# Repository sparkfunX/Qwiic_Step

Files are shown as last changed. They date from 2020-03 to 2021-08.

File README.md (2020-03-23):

SparkX Qwiic Step
========================================

Qwiic Step (https://cdn.sparkfun.com/assets/parts/1/4/5/9/9/15951-Qwiic_Step-01.jpg)

Qwiic Step System (https://cdn.sparkfun.com/assets/parts/1/4/5/9/9/15951-Qwiic_Step-05.jpg)

[*SparkX Qwiic Step (SPX-15951)*](https://www.sparkfun.com/products/15951)

Qwiic Step features the A4988 stepper motor driver IC. Send commands using the I2C bus to configure your stepper motor movements. Easily attach and set up a limit switch or E-Stop and use our new favorite latching terminals to solderlessly and screwlessly attach motor and power.

Repository Contents
-------------------

* **/Documentation** - Data sheets, additional product information
* **/Firmware** - Firmware used on Qwiic Step
* **/Hardware** - Eagle design files (.brd, .sch)
* **/Production** - Production panel files (.brd)

Documentation
--------------
* **[SparkFun Qwiic Step Arduino Library](https://github.com/sparkfun/SparkFun_Qwiic_Step_Arduino_Library)** - Arduino library for the SparkX Qwiic Step.
* **[SparkFun Fritzing repo](https://github.com/sparkfun/Fritzing_Parts)** - Fritzing diagrams for SparkFun products.
* **[SparkFun 3D Model repo](https://github.com/sparkfun/3D_Models)** - 3D models of SparkFun products. 
* **[SparkFun Graphical Datasheets](https://github.com/sparkfun/Graphical_Datasheets)** -Graphical Datasheets for various SparkFun products.

License Information
-------------------

This product is _**open source**_! 

Please review the LICENSE.md file for license information. 

If you have any questions or concerns on licensing, please contact technical support on our [SparkFun forums](https://forum.sparkfun.com/viewforum.php?f=152).

Distributed as-is; no warranty is given.

- Your friends at SparkFun.

_<COLLABORATION CREDIT>_

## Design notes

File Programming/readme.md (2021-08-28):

Programming Qwiic Step
===========================================================

The Qwiic Step uses the ATmega328P with the standard Arduino/STK500 bootloader. New firmware can be loaded with a USB to serial connection and a 6-pin header.

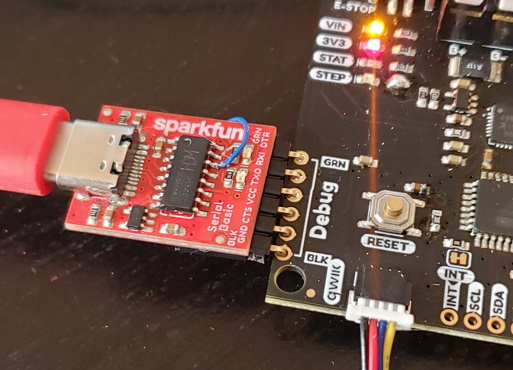
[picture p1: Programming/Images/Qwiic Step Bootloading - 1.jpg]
Programming Qwiic Step via 6-pin Serial


1) Solder a 6-pin [right angle](https://www.sparkfun.com/products/553) (or [straight](https://www.sparkfun.com/products/116)) male header onto the 'Debug' footprint.
2) Connect a [USB to Serial](https://www.sparkfun.com/products/15096) adapter along with a [USB cable](https://www.sparkfun.com/products/15425) to a computer and verify the new COM port is displayed. For information about drivers or COM port locating, see [here](https://learn.sparkfun.com/tutorials/sparkfun-serial-basic-ch340c-hookup-guide).
3) Download the contents of the 'Programming' folder so that you have **avrdude.exe**, **avrdude.conf**, **program_qwiic_step.bat**, and **Qwiic-Step-vXX.hex** in a folder.
4) Modify 'program_qwiic_step.bat' to use the COM port that your computer uses (default is COM5).
5) Open a command line, navigate to 'program_qwiic_step.bat' and run. 
6) Press enter to begin programming.

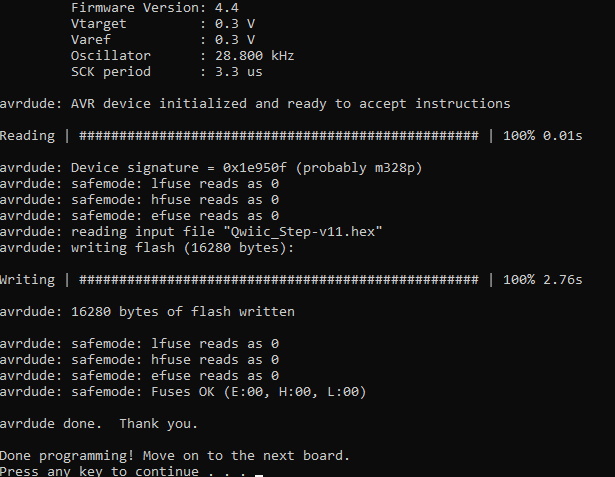
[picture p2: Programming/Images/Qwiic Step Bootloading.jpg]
Output from avrdude


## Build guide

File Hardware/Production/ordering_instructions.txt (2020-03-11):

panel size, 124x116mm
PCB thickness, 1.6mm
number of layers, 4
soldermask color, Black
silkscreen color, White
oz copper, 1oz
finish, HASL lead free
stencils, top+bottom
pcs per panel, 4
min trace width, 0.2032mm / 0.0080in
min drill size, 0.3810mm / 0.0150in
filename to layer stackup 1/2/3/4: GTL, GL2, GL3, GBL

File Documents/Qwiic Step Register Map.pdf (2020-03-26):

# Qwiic Step Register Map

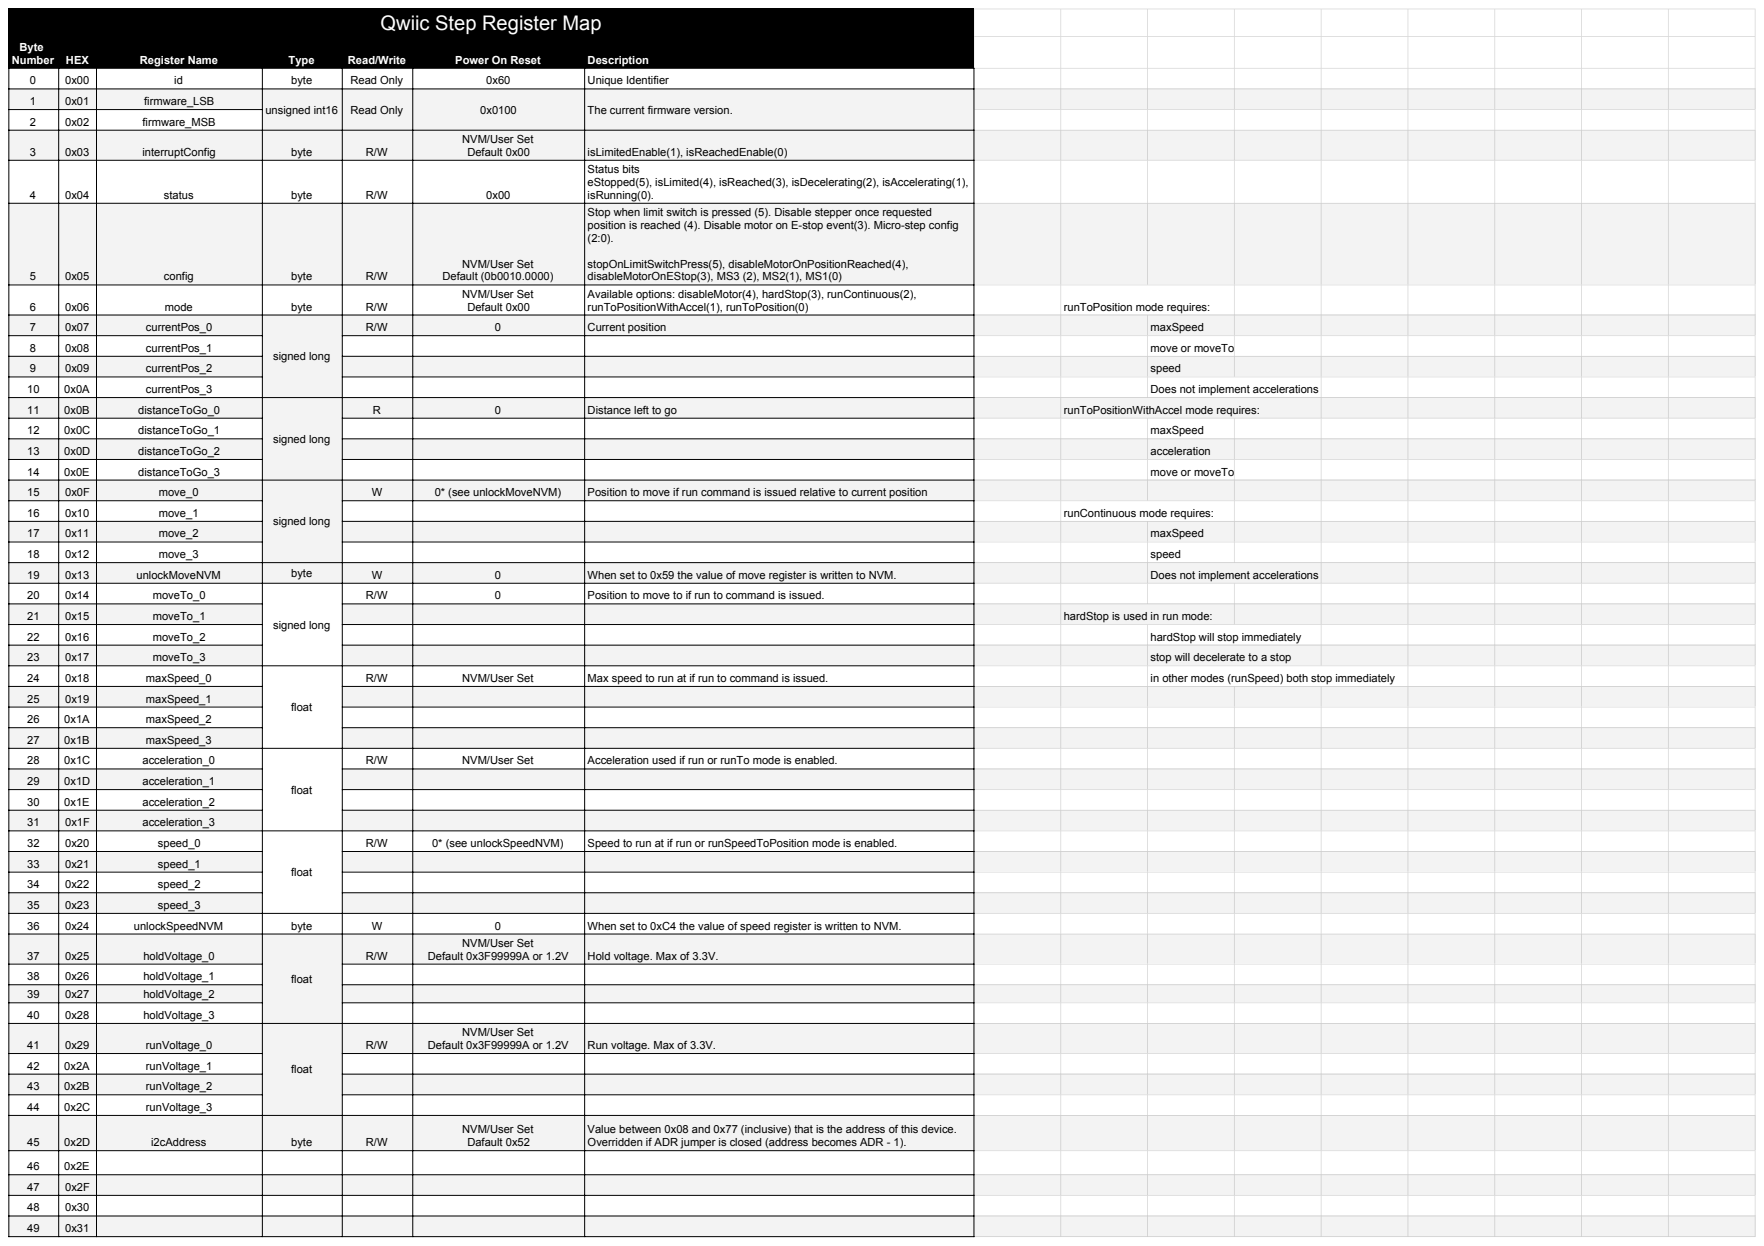
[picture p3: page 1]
Byte Number HEX; Register Name; Type; Read/Write; Power On Reset; Description; runToPositionWithAccel(1), runToPosition(0); runToPosition mode requires:; Current position; maxSpeed; currentPos_1; move or moveTo; currentPos_2; speed; currentPos_3; Does not implement accelerations; distanceToGo_0; signed long; Distance left to go; runToPositionWithAccel mode requires:; distanceToGo_1; distanceToGo_2; acceleration; distanceToGo_3; move_0; 0* (see unlockMoveNVM)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

0 | 0x00 | id | byte | Read Only | 0x60 | Unique Identifier

1 | 0x01 | firmware_LSB | unsigned int16 | Read Only | 0x0100 | The current firmware version. 2
0x02 | firmware_MSB

3 | 0x03 | interruptConfig | byte | R/W | NVM/User Set Default 0x00 | isLimitedEnable(1), isReachedEnable(0)

4 | 0x04 | status | byte | R/W | 0x00 | Status bits eStopped(5), isLimited(4), isReached(3), isDecelerating(2), isAccelerating(1), isRunning(0).

5 | 0x05 | config | byte | R/W | NVM/User Set Default (0b0010.0000) | Stop when limit switch is pressed (5). Disable stepper once requested position is reached (4). Disable motor on E-stop event(3). Micro-step config (2:0). stopOnLimitSwitchPress(5), disableMotorOnPositionReached(4), disableMotorOnEStop(3), MS3 (2), MS2(1), MS1(0)

6 | 0x06 | mode | byte | R/W | NVM/User Set Default 0x00 | Available options: disableMotor(4), hardStop(3), runContinuous(2),

7 | 0x07 | currentPos_0 | signed long

24 | 0x18 | maxSpeed_0 | float

25 | 0x19 | maxSpeed_1

26 | 0x1A | maxSpeed_2

27 | 0x1B | maxSpeed_3

28 | 0x1C | acceleration_0 | float | R/W | NVM/User Set | Acceleration used if run or runTo mode is enabled.

29 | 0x1D | acceleration_1

30 | 0x1E | acceleration_2

31 | 0x1F | acceleration_3

32 | 0x20 | speed_0 | float | R/W | 0* (see unlockSpeedNVM) | Speed to run at if run or runSpeedToPosition mode is enabled.

33 | 0x21 | speed_1

34 | 0x22 | speed_2

35 | 0x23 | speed_3

36 | 0x24 | unlockSpeedNVM | byte | W | 0 | When set to 0xC4 the value of speed register is written to NVM.
37 | 0x25 | holdVoltage_0 | float | R/W | NVM/User Set Default 0x3F99999A or 1.2V | Hold voltage. Max of 3.3V.

38 | 0x26 | holdVoltage_1
39 | 0x27 | holdVoltage_2

40 | 0x28 | holdVoltage_3
41 | 0x29 | runVoltage_0 | float | R/W | NVM/User Set Default 0x3F99999A or 1.2V | Run voltage. Max of 3.3V.

42 | 0x2A | runVoltage_1

43 | 0x2B | runVoltage_2

44 | 0x2C | runVoltage_3

45 | 0x2D | i2cAddress | byte | R/W | NVM/User Set Dafault 0x52 | Value between 0x08 and 0x77 (inclusive) that is the address of this device. Overridden if ADR jumper is closed (address becomes ADR - 1).

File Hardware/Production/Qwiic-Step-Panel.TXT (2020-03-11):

%
M48
M72
T01C0.0150
T02C0.0200
T03C0.0230
T04C0.0400
T05C0.0591
T06C0.0800
T07C0.1300
%
T01
X7875Y4350
X8675Y4350
X10875Y4595
X12375Y3950
X13325Y3950
X13875Y4800
X13420Y5205
X14025Y6100
X14388Y6363
X14675Y6650
X14930Y6350
X15675Y5850
X15525Y5400
X14925Y5400
X13075Y6355
X11375Y6200
X10625Y6700
X10525Y7100
X11375Y7850
X11675Y8350
X11425Y8900
X10875Y9850
X10375Y10145
X11330Y10245
X12225Y10400
X12770Y9850
X13880Y9850
X14675Y9950
X15975Y10900
X16270Y10286
X16675Y10300
X16075Y9050
X16075Y8400
X17188Y8403
X18075Y8200
X18425Y8900
X19275Y8450
X17675Y7100
X16875Y6800
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

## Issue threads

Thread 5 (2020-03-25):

Additions/changes for next rev (X03?)

pmakin-png, 2020-03-25:
* Need voltage regulator on-board to generate 3.3V for proper headless operation
* Add pull-up to ADR jumper or move it

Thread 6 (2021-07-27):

Sending certain values to moveTo causes hang

JamesNikkel, 2021-07-27:
### Subject of the issue
When sending values to moveTo() the integers 1777 and 3555 cause the board to hang.

### Your workbench

Board is attached to Sparkfun Pro Micro Qwiic
Power is via 12V PS (regulated down to 5V for the Pro Micro)
Qwiic Step library version 2.0.1
Arduino IDE 1.8.15

I've bypassed this by noting these 2 failure values, and increment by 1, and it works great, but I'm concerned there may be more values that crop up that I've not found.

void mv_motor(long target)
{
  if ((target == 1777) || (target == 3555) )
    target+=1;
  motor.moveTo(target);
}

### Steps to reproduce
QwiicStep motor;
motor.begin();
motor.setHoldVoltage(0.05);
motor.setRunVoltage(1.10);
motor.setStepSize(STEPSIZE_SIXTEENTH);
motor.setModeRunWithAcceleration();
motor.setSpeed(500);
motor.setAcceleration(100);
motor.clearEStop();
motor.enable();
motor.moveTo(1777);

### Expected behavior
motor should just move to 1777

### Actual behavior
board becomes un-responsive, system hangs

nseidle, 2021-08-28:
Whew. This was a hard one to track down. I'm not convinced I have the culprit but I think I'm close.

For each setting (setHoldVoltage, setSpeed, etc) Qwiic Step is writing the setting to EEPROM in the I2C ISR. EEPROM is slow, and can take 10s of ms to write. Because the master is throwing multiple settings at QS in repetition, Qwiis Step is not receiving all the commands. And, while I can't replicate the exact lock up behavior, I can see the I2C bus taking a dive with an ESP32. I suspect the ATmega328 is clock stretching the I2C bus very badly while it waits for the EEPROM writes to complete.

The solution is to move the EEPROM writes outside the ISR (where they probably should have been in the first place). I've tested this and the I2C lockups go away. If you're interested, I can send you a new Qwiic Step firmware version to test.

JamesNikkel, 2021-08-28:
That's great!  I though I may have been going mad (the fact that it always seemed to fail only when the last three (decimal) digits repeated was just not something I could wrap my head around).  I'd be happy to test a new firmware when it is available.

nseidle, 2021-08-28:
I really hate delay hacks, but a work around for the firmware you have should be ~20ms delay between each command sends:

    int qsSettingDelay = 20;
    motor.setSpeed(400);
    delay(qsSettingDelay);
    motor.setHoldVoltage(0.03); //POR of QS is 0.05 and 1.2 so that's not the issue
    delay(qsSettingDelay);
    motor.setRunVoltage(1.10);
    delay(qsSettingDelay);
    motor.setModeRunWithAcceleration();
    delay(qsSettingDelay);
    motor.setAcceleration(200);
    delay(qsSettingDelay);
    motor.clearEStop();
    delay(qsSettingDelay);
    motor.enable();
    delay(qsSettingDelay);
    motor.moveTo(1777);

This works but I'm still seeing some bad I2C transactions. I'll get new firmware and programming instructions shortly.

nseidle, 2021-08-28:
Ok, the programming instructions are [here](https://github.com/sparkfunX/Qwiic_Step/tree/master/Programming) as well as new v11 firmware. Please give programming a try and let me know if you have issues or see improvements.

JamesNikkel, 2022-11-11:
Hi Nathan,

I know it’s been a while, but the device that the stepper driver is in has been at use in an x-ray lab for the last year or so, and I just got it back for refurbishment.  So my hack to just avoid a few values worked well enough for them.  :)

I updated to the firmware that you provided, and that may have cleaned it up a little bit, but in the complete system with the remote switch controls (Using those QwiicBus over cat5 cable)  it would still hang at various specific moveTo values.

Realizing it had something to do with the overall i2c environment, I changed out the Qwiic Pro Micro to a Samd21E Qwiic Micro, and now it works perfectly with no added hacks.

In any event, thank you for your help, if you ever make these things again, looks like a couple tweaks may be order, but this one now seems pretty solid.

Cheers,
James

----
James Nikkel
Advanced Prototyping Centre
https://advancedprototyping.yale.edu
Wright Laboratory
Yale University

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

nseidle, 2022-11-14:
Glad to hear it! Thanks for reporting back.

We don't have plans for a revision at this time but I'm thrilled to hear it helped your prototyping.

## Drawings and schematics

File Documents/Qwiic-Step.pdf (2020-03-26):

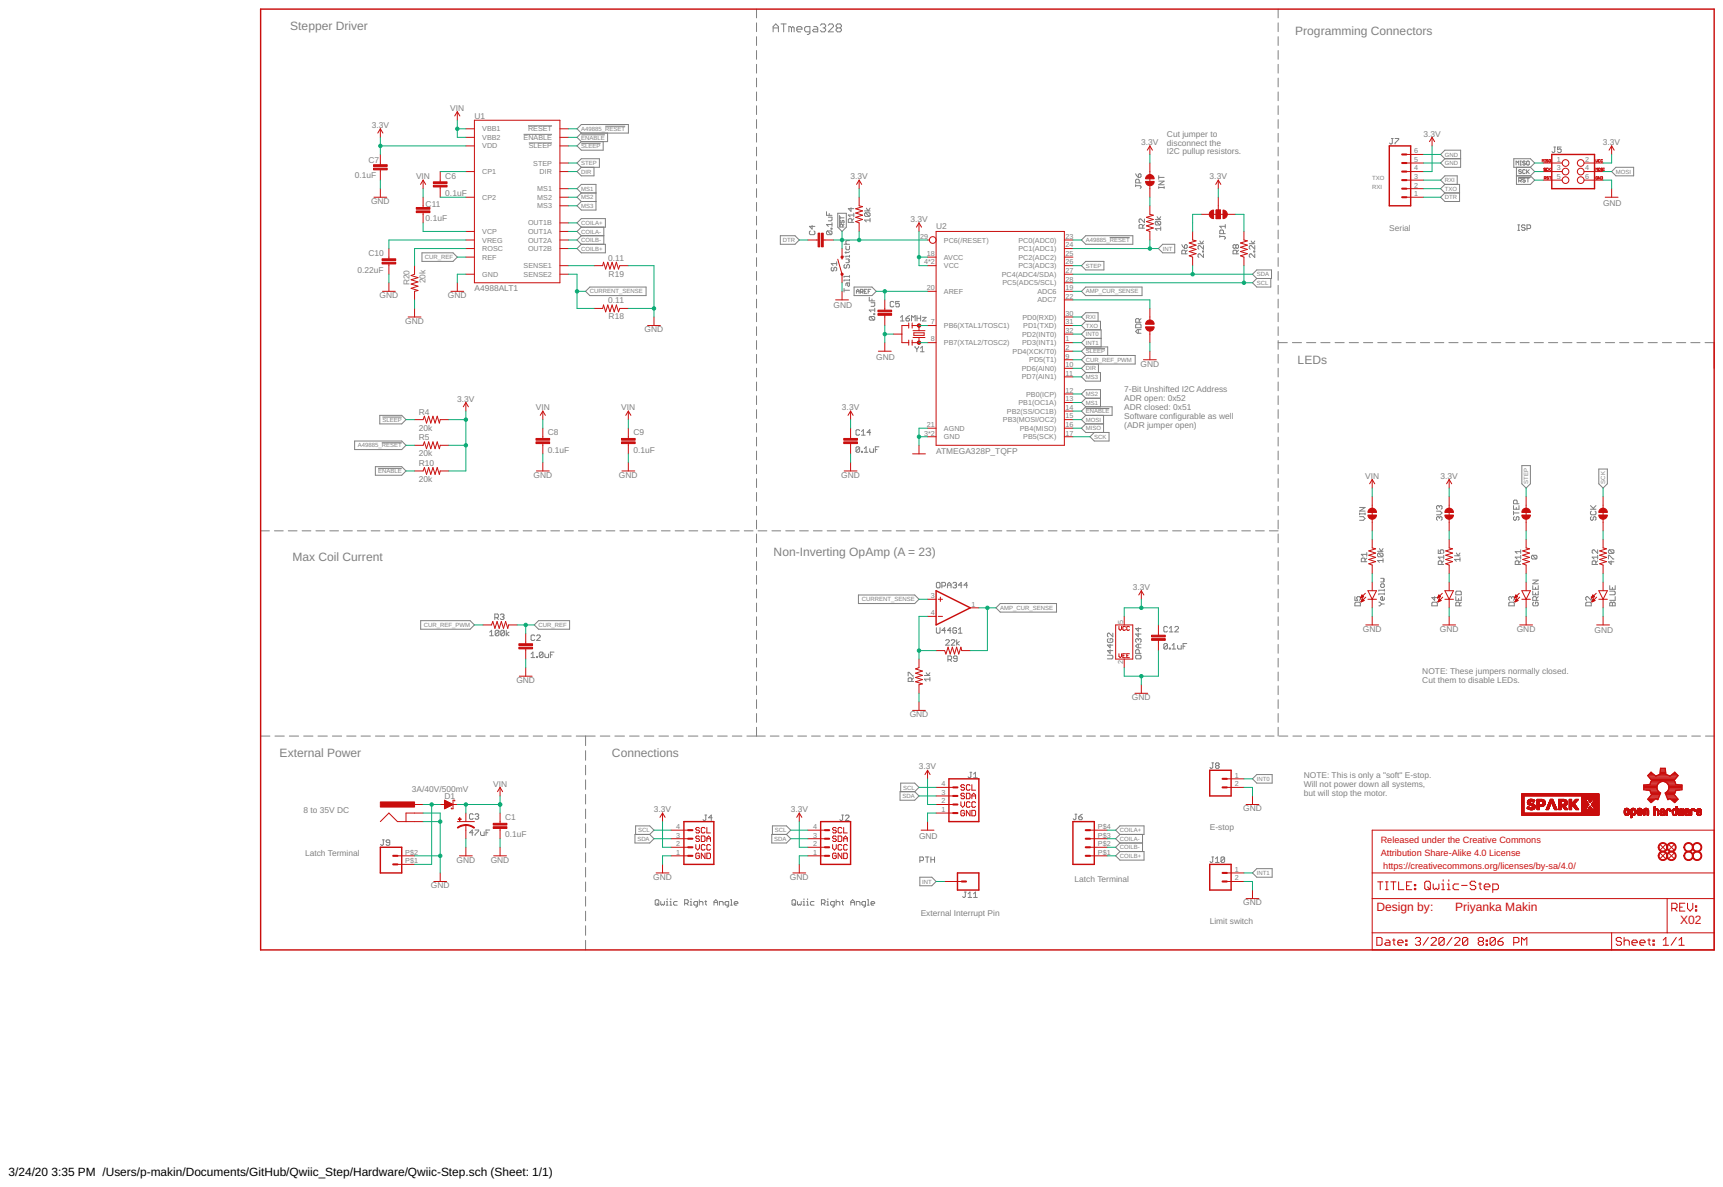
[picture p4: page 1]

PB4(MISO) 16 PB3(MOSI/OC2) 15 PB2(SS/OC1B) 14 PB1(OC1A) 13 PB0(ICP) 12 PD7(AIN1) 11 PD6(AIN0) 10 PD5(T1) 9 PD4(XCK/T0) 2 PD3(INT1) 1 PD2(INT0) 32 PD1(TXD) 31 PD0(RXD) 30 ADC7

7-Bit Unshifted I2C Address ADR open: 0x52
ADR closed: 0x51
Software configurable as well
(ADR jumper open)

NOTE: These jumpers normally closed. Cut them to disable LEDs.

NOTE: This is only a "soft" E-stop. Will not power down all systems, but will stop the motor.

Released under the Creative Commons Attribution Share-Alike 4.0 License

https://creativecommons.org/licenses/by-sa/4.0/

3/24/20 3:35 PM /Users/p-makin/Documents/GitHub/Qwiic_Step/Hardware/Qwiic-Step.sch (Sheet: 1/1)

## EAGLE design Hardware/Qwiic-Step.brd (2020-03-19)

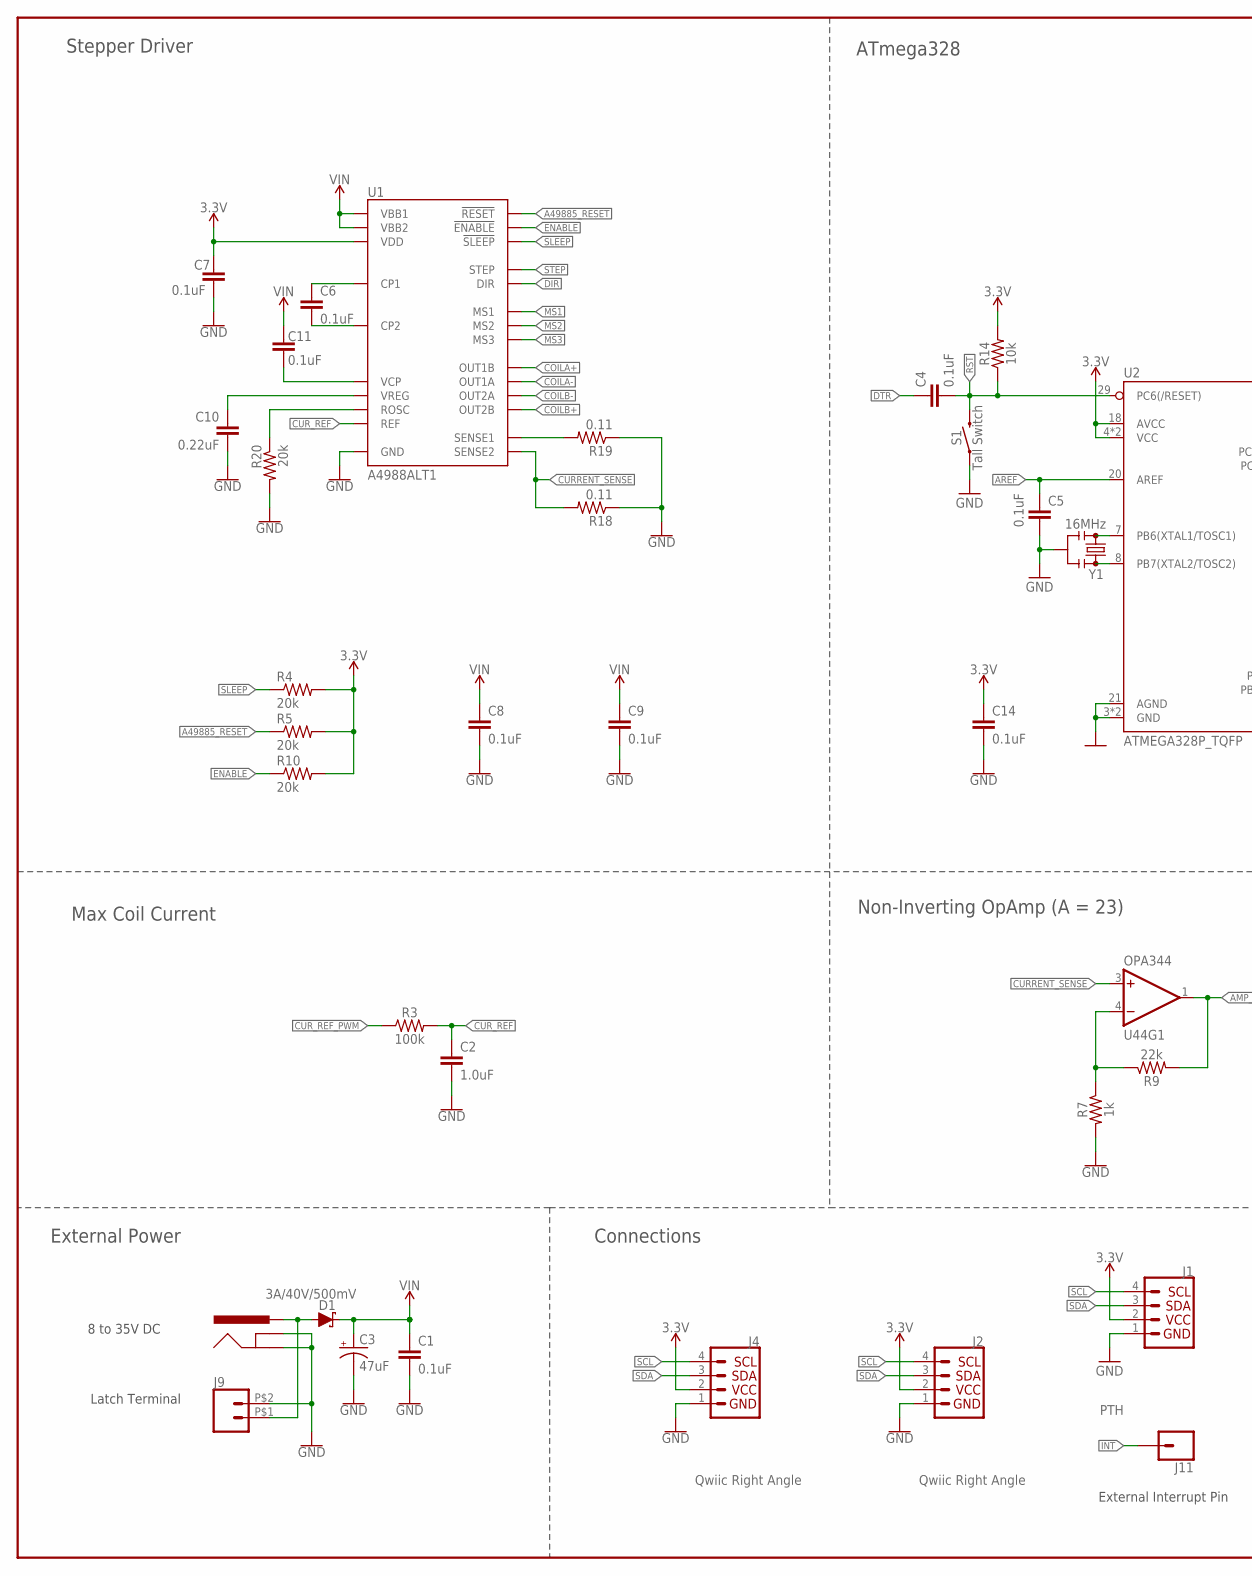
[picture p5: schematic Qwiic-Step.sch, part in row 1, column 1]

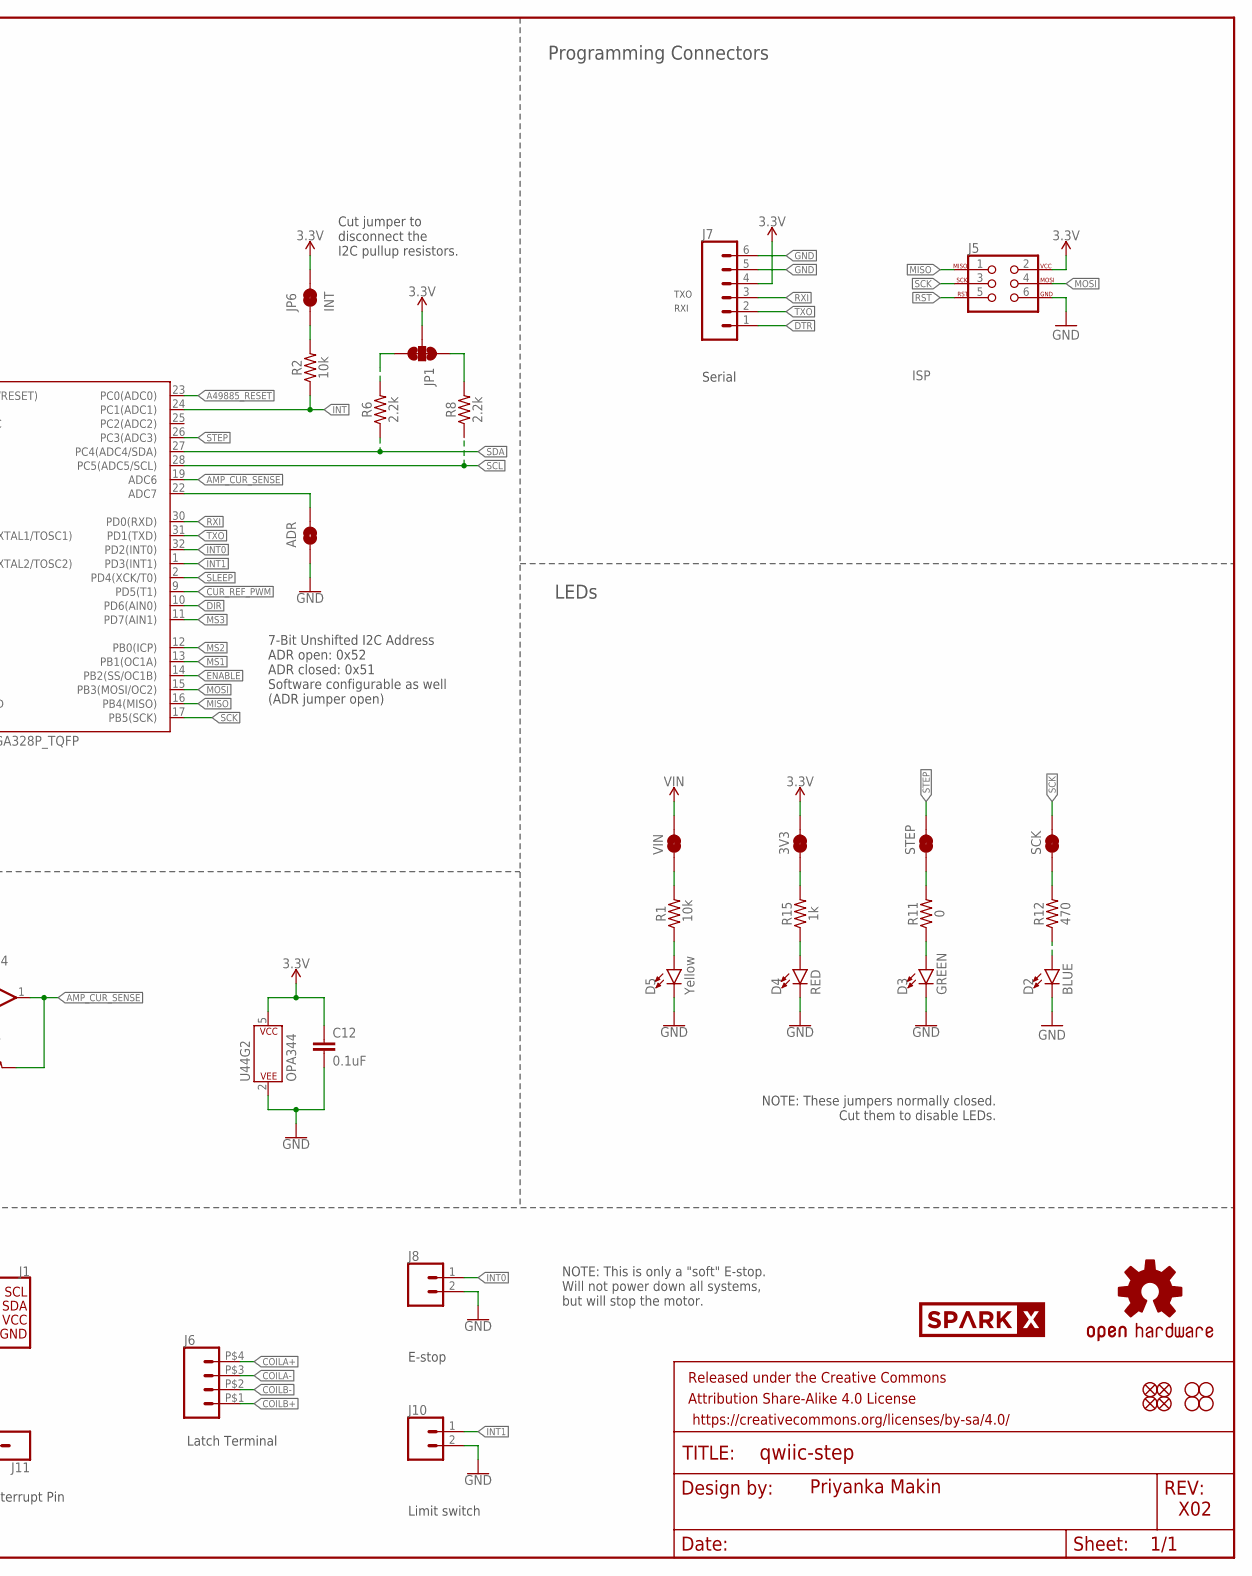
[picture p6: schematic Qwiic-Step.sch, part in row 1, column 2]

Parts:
3V3: JUMPER-SMT_2_NC_TRACE_SILK; SMT-JUMPER_2_NC_TRACE_SILK
ADR: ADR; SMT-JUMPER_2_NO_SILK
C1, C4, C5, C6, C7, C8, C9, C11, C12, C14: 0.1uF; 0603
C2: 1.0uF; 0603
C3: 47uF; PANASONIC_D
C10: 0.22uF; 0603
D1: 3A/40V/500mV; SMA-DIODE
D2: BLUE; LED-0603
D3: GREEN; LED-0603
D4: RED; LED-0603
D5: Yellow; LED-0603
FD1, FD2, FD3, FD4: FIDUCIAL1X2; FIDUCIAL-1X2
FRAME2: FRAME-LEDGER; CREATIVE_COMMONS
J1: PTH; 1X04_NO_SILK
J2, J4: Qwiic Right Angle; JST04_1MM_RA
J3: 5.5x2.1mm Barrel; POWER_JACK_SMD
J5: ISP; 2X3_TEST_POINTS
J6: CONN_04LATCH; LATCHTERMINAL-5MM-4
J7: CONN_06NO_SILK_NO_POP; 1X06_NO_SILK
J8, J10: CONN_02-JST-2MM-SMT; JST-2-SMD
J9: CONN_02LATCH_2; LATCHTERMINAL-5MM-2
J11: CONN_01PTH_NO_SILK_YES_STOP; 1X01_NO_SILK
JP1: JUMPER-SMT_3_2-NC_TRACE_SILK; SMT-JUMPER_3_2-NC_TRACE_SILK
JP6: INT; SMT-JUMPER_2_NC_TRACE_SILK
JP7, JP8, JP9, JP10: STAND-OFF
LOGO1: OSHW-LOGOMINI; OSHW-LOGO-MINI
R1, R2, R14: 10k; 0603
R3: 100k; 0603
R4, R5, R10, R20: 20k; 0603
R6, R8: 2.2k; 0603
R7, R15: 1k; 0603
R9: 22k; 0603
R11: 0; 0603
R12: 470; 0603
R18, R19: 0.11; 2010
S1: Tall Switch; TACTILE_SWITCH_SMD_5.2MM
SCK: JUMPER-SMT_2_NC_TRACE_SILK; SMT-JUMPER_2_NC_TRACE_SILK
STEP: JUMPER-SMT_2_NC_TRACE_SILK; SMT-JUMPER_2_NC_TRACE_SILK
U1: A4988ALT1; QFN-28-5MM
U2: ATMEGA328P_TQFP; TQFP32-08
U44: OPA344; SOT23-5
U$49: SPARKX-LOGO4; SPARKX-MEDIUM
VIN: JUMPER-SMT_2_NC_TRACE_SILK; SMT-JUMPER_2_NC_TRACE_SILK
Y1: 16MHz; RESONATOR-SMD-3.2X1.3

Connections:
3.3V: 3V3.2, C7.1, C12.1, C14.1, J1.2 (VCC), J2.2, J4.2, J5.2, J7.4, JP1.2, JP6.2, R4.2, R5.2, R10.2, R14.2, U1.15 (VDD), U2.4 (VCC), U2.6 (VCC), U2.18 (AVCC), U44.5 (P$V+)
!ENABLE!: R10.1, U1.2 (!ENABLE!), U2.14 (PB2(SS/OC1B))
!RST!: C4.2, J5.5, R14.1, S1.3 (2), S1.4 (2), U2.29 (PC6(/RESET))
!SLEEP!: R4.1, U1.14 (!SLEEP!), U2.2 (PD4(XCK/T0))
A49885_!RESET!: R5.1, U1.12 (!RESET!), U2.23 (PC0(ADC0))
AMP_CUR_SENSE: R9.2, U2.19 (ADC6), U44.1 (OUT)
AREF: C5.1, U2.20 (AREF)
COILA+: J6.P$4 (4), U1.21 (OUT1B)
COILA-: J6.P$3 (3), U1.24 (OUT1A)
COILB+: J6.P$1 (1), U1.1 (OUT2B)
COILB-: J6.P$2 (2), U1.26 (OUT2A)
CURRENT_SENSE: R18.2, U1.27 (SENSE2), U44.3 (+IN)
CUR_REF: C2.1, R3.2, U1.17 (REF)
CUR_REF_PWM: R3.1, U2.9 (PD5(T1))
DIR: U1.19 (DIR), U2.10 (PD6(AIN0))
DTR: C4.1, J7.1
GND: ADR.2, C1.2, C2.2, C3.-, C5.2, C7.2, C8.2, C9.2, C10.2, C12.2, C14.2, D2.C, D3.C, D4.C, D5.C, J1.1 (GND), J2.1, J3.GND (GNDBREAK), J3.P$4 (GND), J4.1, J5.6, J7.5, J7.6, J8.2 (1), J9.P$2 (2), J10.2 (1), R7.2, R18.1, R19.1, R20.2, S1.1, S1.2 (1), U1.3 (GND), U1.18 (GND), U1.29 (GND), U2.3 (GND), U2.5 (GND), U2.21 (AGND), U44.2 (P$V-), Y1.2
INT: J11.1, R2.1, U2.24 (PC1(ADC1))
INT0: J8.1 (2), U2.32 (PD2(INT0))
INT1: J10.1 (2), U2.1 (PD3(INT1))
MISO: J5.1, U2.16 (PB4(MISO))
MOSI: J5.4, U2.15 (PB3(MOSI/OC2))
MS1: U1.9 (MS1), U2.13 (PB1(OC1A))
MS2: U1.10 (MS2), U2.12 (PB0(ICP))
MS3: U1.11 (MS3), U2.11 (PD7(AIN1))
unnamed: D3.A, R11.1
unnamed: R7.1, R9.1, U44.4 (-IN)
unnamed: R19.2, U1.23 (SENSE1)
unnamed: R1.2, VIN.1
unnamed: JP6.1, R2.2
unnamed: ADR.1, U2.22 (ADC7)
unnamed: D1.A, J3.VIN0 (PWR), J9.P$1 (1)
unnamed: C6.1, U1.4 (CP1)
unnamed: C6.2, U1.5 (CP2)
unnamed: D5.A, R1.1
unnamed: R11.2, STEP.1
unnamed: D2.A, R12.1
unnamed: U2.7 (PB6(XTAL1/TOSC1)), Y1.1
unnamed: U2.8 (PB7(XTAL2/TOSC2)), Y1.3
unnamed: JP1.3, R6.2
unnamed: JP1.1, R8.2
unnamed: R12.2, SCK.1
unnamed: R20.1, U1.13 (ROSC)
unnamed: C10.1, U1.8 (VREG)
unnamed: C11.1, U1.6 (VCP)
unnamed: D4.A, R15.1
unnamed: 3V3.1, R15.2
RXI: J7.3, U2.30 (PD0(RXD))
SCK: J5.3, SCK.2, U2.17 (PB5(SCK))
SCL: J1.4 (SCL), J2.4, J4.4, R8.1, U2.28 (PC5(ADC5/SCL))
SDA: J1.3 (SDA), J2.3, J4.3, R6.1, U2.27 (PC4(ADC4/SDA))
STEP: STEP.2, U1.16 (STEP), U2.26 (PC3(ADC3))
TXO: J7.2, U2.31 (PD1(TXD))
VIN: C1.1, C3.+, C8.1, C9.1, C11.2, D1.C, U1.22 (VBB1), U1.28 (VBB2), VIN.2

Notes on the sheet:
8 to 35V DC
Stepper Driver
Connections
Max Coil Current
External Power
ATmega328
TXO
RXI
Limit switch
E-stop
External Interrupt Pin
Latch Terminal
Priyanka Makin
X02
LEDs
Programming Connectors
Non-Inverting OpAmp (A = 23)
Serial
NOTE: These jumpers normally closed. Cut them to disable LEDs.
NOTE: This is only a "soft" E-stop. Will not power down all systems, but will stop the motor.
7-Bit Unshifted I2C Address ADR open: 0x52 ADR closed: 0x51 Software configurable as well (ADR jumper open)
Cut jumper to disconnect the I2C pullup resistors.

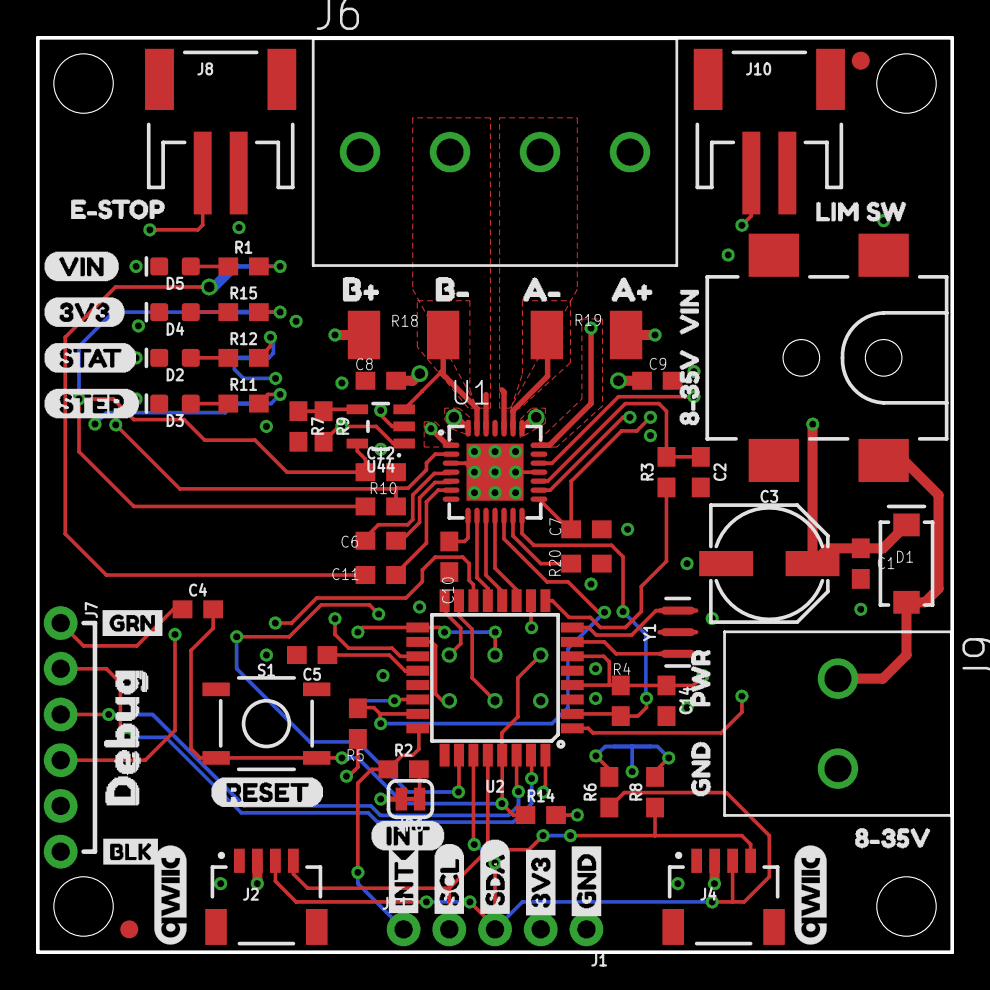
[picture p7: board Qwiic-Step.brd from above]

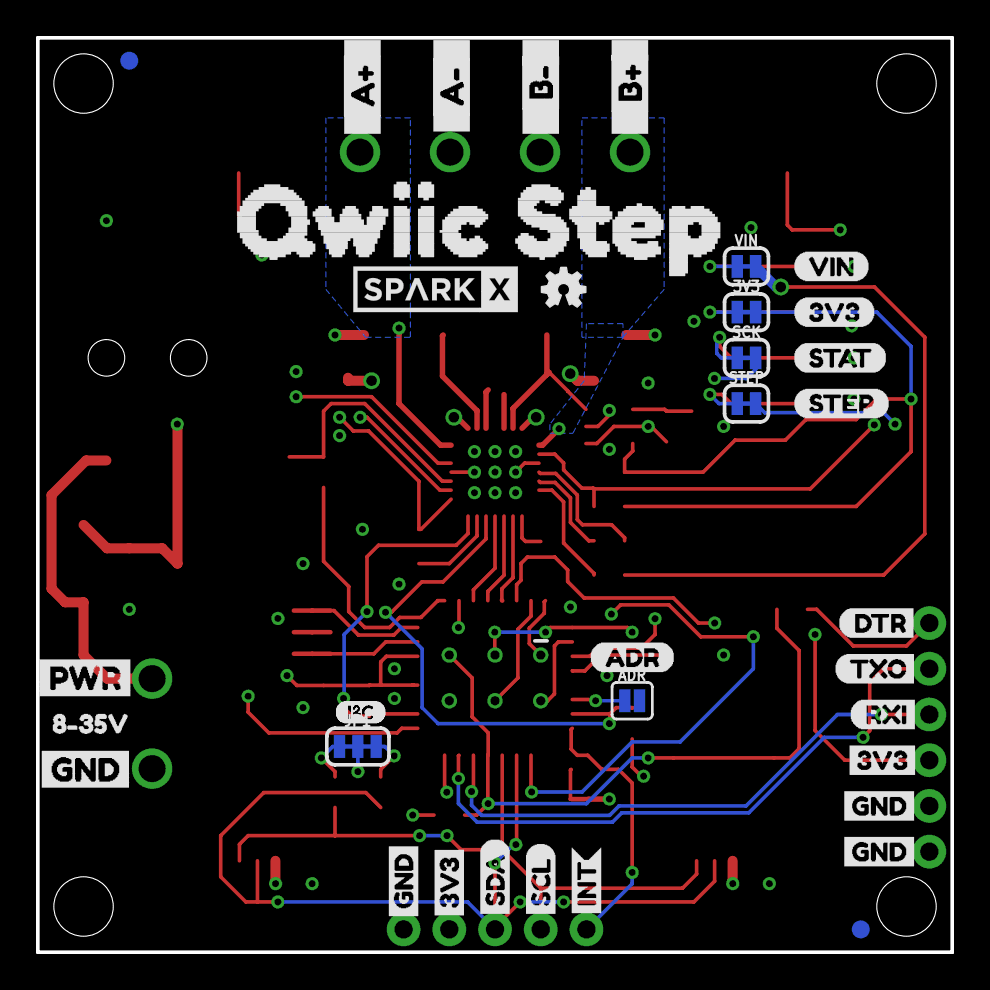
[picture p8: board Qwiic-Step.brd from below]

Board: 4 copper layers, 50.8 x 50.8 mm, 122 parts (37 on the bottom side), 54 nets.

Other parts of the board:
U$1: 3V30
U$2: 3V37
U$3: GND8
U$4: STAT5
U$5: SCL5
U$6: SDA6
U$7: STEP4
U$8: VIN3
U$9, U$29: QWIIC_5.5MM
U$10, U$11, U$40: 8#35V0
U$12: VIN1
U$13: STAT0
U$14: E#STOP2
U$15, U$16: I_SUPER2_C-()-03
U$17, U$45: 3V31
U$18: DTR4
U$19: DEBUG0
U$20: BLK2
U$21, U$22, U$44: GND0
U$23: LIM_SW3
U$24, U$30: INT4
U$25: ADR0
U$26: 3V35
U$27: RESET1
U$28: GRN1
U$31: GND6
U$32, U$54: A#2
U$33: SDA4
U$34: SCL3
U$35: RXI3
U$36, U$55: A#3
U$37: STEP2
U$38: VIN0
U$41: INT2
U$42: GND1
U$43: PWR0
U$46, U$57: B#4
U$47, U$58: B#5
U$48: TXO2
U$53: PWR1
U$56: QWIIC_STEP0

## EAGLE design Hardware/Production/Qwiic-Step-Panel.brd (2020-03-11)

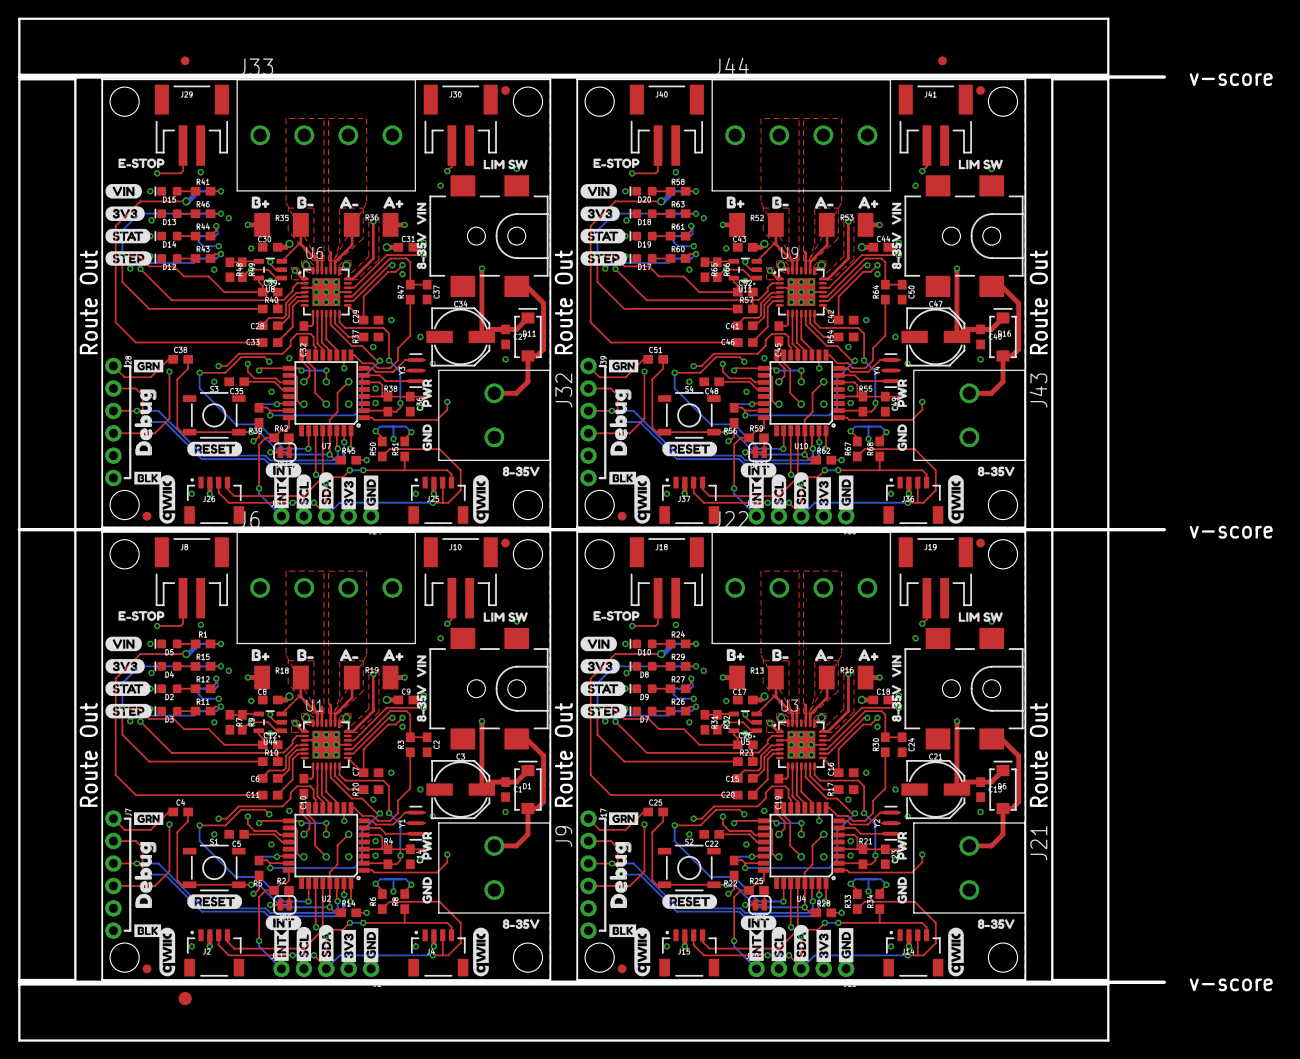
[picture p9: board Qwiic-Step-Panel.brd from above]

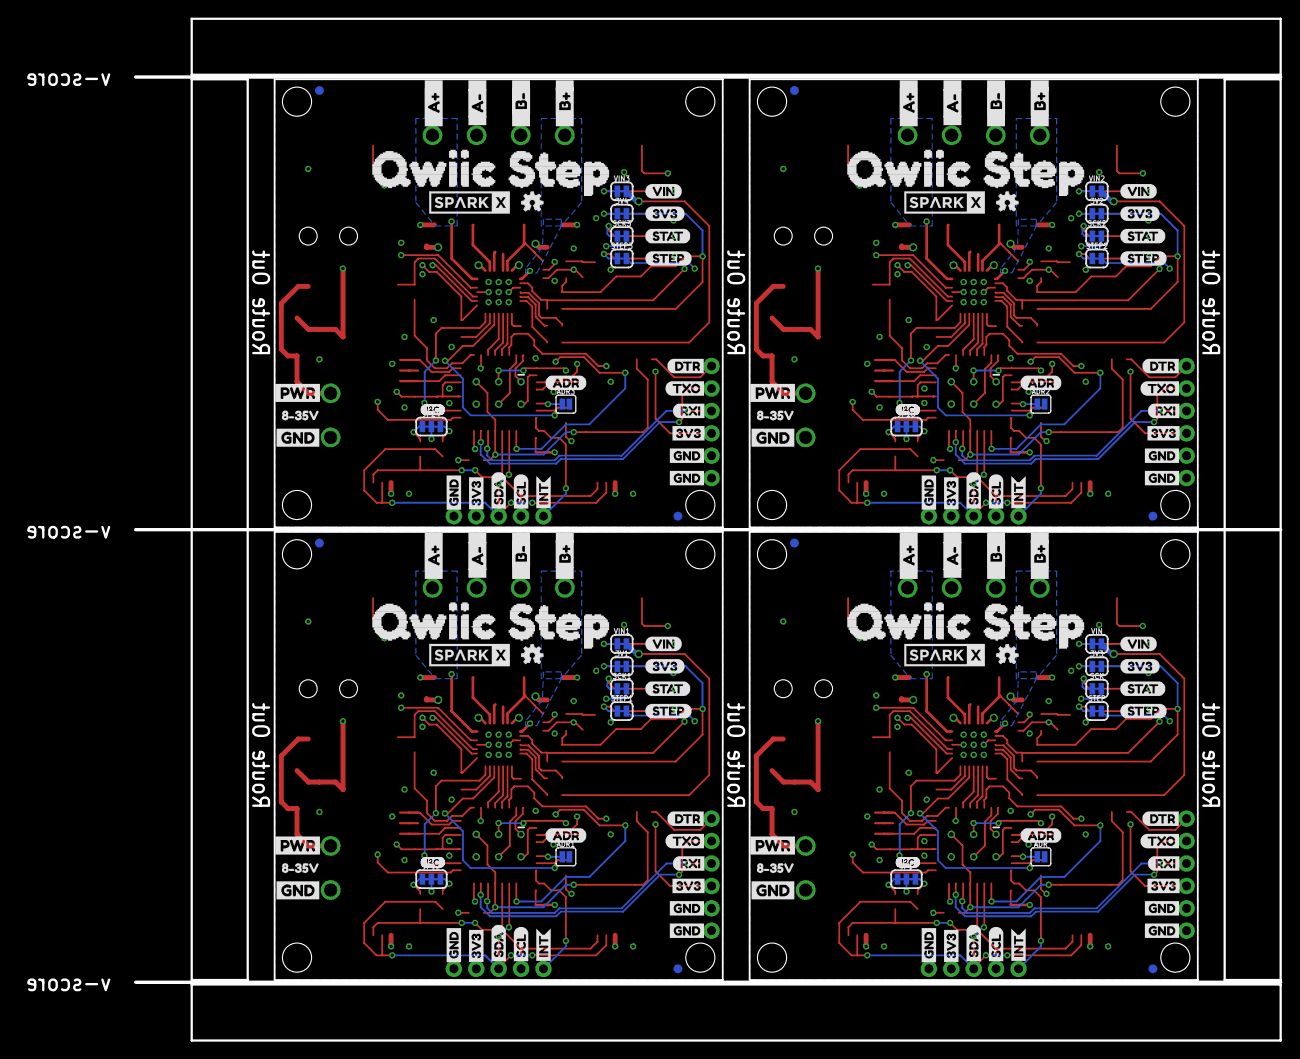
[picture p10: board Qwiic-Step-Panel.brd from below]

Board: 4 copper layers, 129.8 x 115.8 mm, 487 parts (148 on the bottom side), 216 nets.

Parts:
3V1, 3V2, 3V3, 3V4: JUMPER-SMT_2_NC_TRACE_SILK; SMT-JUMPER_2_NC_TRACE_SILK
ADR, ADR1, ADR2, ADR3: ADR; SMT-JUMPER_2_NO_SILK
C1, C4, C5, C6, C7, C8, C9, C11, C12, C13, C14, C15, C16, C17, C18, C20, C22, C23, C25, C26, C27, C28, C29, C30, C31, C33, C35, C36, C38, C39, C40, C41, C42, C43, C44, C46, C48, C49, C51, C52: 0.1uF; 0603
C2, C24, C37, C50: 10nF; 0603
C3, C21, C34, C47: 47uF; PANASONIC_D
C10, C19, C32, C45: 0.22uF; 0603
D1, D6, D11, D16: 3A/40V/500mV; SMA-DIODE
D2, D9, D14, D19: BLUE; LED-0603
D3, D7, D12, D17: GREEN; LED-0603
D4, D8, D13, D18: RED; LED-0603
D5, D10, D15, D20: Yellow; LED-0603
E$1, E$2: FIDUCIAL-1X2
E$3: FIDUCIAL-1.5X3
FD1, FD2, FD3, FD4, FD5, FD6, FD7, FD8, FD9, FD10, FD11, FD12, FD13, FD14, FD15, FD16: FIDUCIAL1X2; FIDUCIAL-1X2
J1, J13, J24, J35: PTH; 1X04_NO_SILK
J2, J4, J14, J15, J25, J26, J36, J37: Qwiic Right Angle; JST04_1MM_RA
J3, J12, J23, J34: 5.5x2.1mm Barrel; POWER_JACK_SMD
J5, J16, J27, J38: ISP; 2X3_TEST_POINTS
J6, J22, J33, J44: LATCHTERMINAL-5MM-4
J7, J17, J28, J39: 1X06_NO_SILK
J8, J10, J18, J19, J29, J30, J40, J41: JST-2-SMD
J9, J21, J32, J43: LATCHTERMINAL-5MM-2
J11, J20, J31, J42: 1X01_NO_SILK
JP1, JP12, JP18, JP24: SMT-JUMPER_3_2-NC_TRACE_SILK
JP2, JP3, JP5, JP7, JP8, JP9, JP10, JP11, JP13, JP14, JP16, JP17, JP19, JP20, JP22, JP23: STAND-OFF
JP4, JP6, JP15, JP21: INT; SMT-JUMPER_2_NC_TRACE_SILK
LOGO1, LOGO2, LOGO3, LOGO4: OSHW-LOGOMINI; OSHW-LOGO-MINI
R1, R24, R41, R58: 4.7k; 0603
R2, R14, R25, R28, R42, R45, R59, R62: 10k; 0603
R3, R30, R47, R64: 33k; 0603
R4, R5, R10, R17, R20, R21, R22, R23, R37, R38, R39, R40, R54, R55, R56, R57: 20k; 0603
R6, R8, R33, R34, R50, R51, R67, R68: 2.2k; 0603
R7, R11, R15, R26, R29, R31, R43, R46, R48, R60, R63, R65: 1k; 0603
R9, R32, R49, R66: 22k; 0603
R12, R27, R44, R61: 470; 0603
R13, R16, R18, R19, R35, R36, R52, R53: 0.11; 2010
S1, S2, S3, S4: Tall Switch; TACTILE_SWITCH_SMD_5.2MM
SCK, SCK1, SCK2, SCK3: JUMPER-SMT_2_NC_TRACE_SILK; SMT-JUMPER_2_NC_TRACE_SILK
STEP, STEP1, STEP2, STEP3: JUMPER-SMT_2_NC_TRACE_SILK; SMT-JUMPER_2_NC_TRACE_SILK
U1, U3, U6, U9: A4988ALT1; QFN-28-5MM
U2, U4, U7, U10: ATMEGA328P_TQFP; TQFP32-08
U5, U8, U11, U44: OPA344; SOT23-5
U$1, U$39, U$109, U$163: 3V30
U$2, U$50, U$110, U$164: 3V37
U$3, U$51, U$111, U$165: GND8
U$4, U$62, U$116, U$170: STAT5
U$5, U$52, U$112, U$166: SCL5
U$6, U$59, U$113, U$167: SDA6
U$7, U$60, U$114, U$168: STEP4
U$8, U$61, U$115, U$169: VIN3
U$9, U$29, U$65, U$74, U$119, U$128, U$173, U$182: QWIIC_5.5MM
U$10, U$11, U$40, U$66, U$67, U$99, U$120, U$121, U$153, U$174, U$175, U$207: 8#35V0
U$12, U$68, U$122, U$176: VIN1
U$13, U$106, U$160, U$214: STAT0
U$14, U$69, U$123, U$177: E#STOP2
U$15, U$16, U$107, U$108, U$161, U$162, U$215, U$216: I_SUPER2_C-()-03
U$17, U$45, U$83, U$91, U$137, U$145, U$191, U$199: 3V31
U$18, U$92, U$146, U$200: DTR4
U$19, U$98, U$152, U$206: DEBUG0
U$20, U$63, U$117, U$171: BLK2
U$21, U$22, U$44, U$93, U$94, U$100, U$147, U$148, U$154, U$201, U$202, U$208: GND0
U$23, U$70, U$124, U$178: LIM_SW3
U$24, U$30, U$71, U$75, U$125, U$129, U$179, U$183: INT4
U$25, U$72, U$126, U$180: ADR0
U$26, U$76, U$130, U$184: 3V35
U$27, U$73, U$127, U$181: RESET1
U$28, U$64, U$118, U$172: GRN1
U$31, U$77, U$131, U$185: GND6
U$32, U$54, U$87, U$102, U$141, U$156, U$195, U$210: A#2
U$33, U$78, U$132, U$186: SDA4
U$34, U$79, U$133, U$187: SCL3
U$35, U$95, U$149, U$203: RXI3
U$36, U$55, U$88, U$103, U$142, U$157, U$196, U$211: A#3
U$37, U$84, U$138, U$192: STEP2
U$38, U$85, U$139, U$193: VIN0
U$41, U$80, U$134, U$188: INT2
U$42, U$81, U$135, U$189: GND1
U$43, U$82, U$136, U$190: PWR0
U$46, U$57, U$89, U$104, U$143, U$158, U$197, U$212: B#4
U$47, U$58, U$90, U$105, U$144, U$159, U$198, U$213: B#5
U$48, U$96, U$150, U$204: TXO2
U$49, U$97, U$151, U$205: SPARKX-LOGO4; SPARKX-MEDIUM
U$53, U$101, U$155, U$209: PWR1
U$56, U$86, U$140, U$194: QWIIC_STEP0
VIN, VIN1, VIN2, VIN3: JUMPER-SMT_2_NC_TRACE_SILK; SMT-JUMPER_2_NC_TRACE_SILK
Y1, Y2, Y3, Y4: 16MHz; RESONATOR-SMD-3.2X1.3

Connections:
3.3V: 3V3.2, C7.1, C12.1, C14.1, J1.2, J2.2, J4.2, J5.2, J7.4, JP1.2, JP6.2, R4.2, R5.2, R10.2, R14.2, U1.15, U2.4, U2.6, U2.18, U44.5
3.3V1: 3V1.2, C16.1, C23.1, C26.1, J13.2, J14.2, J15.2, J16.2, J17.4, JP4.2, JP12.2, R21.2, R22.2, R23.2, R28.2, U3.15, U4.4, U4.6, U4.18, U5.5
3.3V2: 3V2.2, C29.1, C36.1, C39.1, J24.2, J25.2, J26.2, J27.2, J28.4, JP15.2, JP18.2, R38.2, R39.2, R40.2, R45.2, U6.15, U7.4, U7.6, U7.18, U8.5
3.3V3: 3V4.2, C42.1, C49.1, C52.1, J35.2, J36.2, J37.2, J38.2, J39.4, JP21.2, JP24.2, R55.2, R56.2, R57.2, R62.2, U9.15, U10.4, U10.6, U10.18, U11.5
!ENABLE!: R10.1, U1.2, U2.14
!ENABLE!1: R23.1, U3.2, U4.14
!ENABLE!2: R40.1, U6.2, U7.14
!ENABLE!3: R57.1, U9.2, U10.14
!RST!: C4.2, J5.5, R14.1, S1.3, S1.4, U2.29
!RST!1: C25.2, J16.5, R28.1, S2.3, S2.4, U4.29
!RST!2: C38.2, J27.5, R45.1, S3.3, S3.4, U7.29
!RST!3: C51.2, J38.5, R62.1, S4.3, S4.4, U10.29
!SLEEP!: R4.1, U1.14, U2.2
!SLEEP!1: R21.1, U3.14, U4.2
!SLEEP!2: R38.1, U6.14, U7.2
!SLEEP!3: R55.1, U9.14, U10.2
A49885_!RESET!: R5.1, U1.12, U2.23
A49885_!RESET!1: R22.1, U3.12, U4.23
A49885_!RESET!2: R39.1, U6.12, U7.23
A49885_!RESET!3: R56.1, U9.12, U10.23
AMP_CUR_SENSE: R9.2, U2.19, U44.1
AMP_CUR_SENSE1: R32.2, U4.19, U5.1
AMP_CUR_SENSE2: R49.2, U7.19, U8.1
AMP_CUR_SENSE3: R66.2, U10.19, U11.1
AREF: C5.1, U2.20
AREF1: C22.1, U4.20
AREF2: C35.1, U7.20
AREF3: C48.1, U10.20
COILA+: J6.P$4, U1.21
COILA+1: J22.P$4, U3.21
COILA+2: J33.P$4, U6.21
COILA+3: J44.P$4, U9.21
COILA-: J6.P$3, U1.24
COILA-1: J22.P$3, U3.24
COILA-2: J33.P$3, U6.24
COILA-3: J44.P$3, U9.24
COILB+: J6.P$1, U1.1
COILB+1: J22.P$1, U3.1
COILB+2: J33.P$1, U6.1
COILB+3: J44.P$1, U9.1
COILB-: J6.P$2, U1.26
COILB-1: J22.P$2, U3.26
COILB-2: J33.P$2, U6.26
COILB-3: J44.P$2, U9.26
CURRENT_SENSE: R18.2, U1.27, U44.3
CURRENT_SENSE1: R13.2, U3.27, U5.3
CURRENT_SENSE2: R35.2, U6.27, U8.3
CURRENT_SENSE3: R52.2, U9.27, U11.3
CUR_REF: C2.1, R3.2, U1.17
CUR_REF1: C24.1, R30.2, U3.17
CUR_REF2: C37.1, R47.2, U6.17
CUR_REF3: C50.1, R64.2, U9.17
CUR_REF_PWM: R3.1, U2.9
CUR_REF_PWM1: R30.1, U4.9
CUR_REF_PWM2: R47.1, U7.9
CUR_REF_PWM3: R64.1, U10.9
DIR: U1.19, U2.10
DIR1: U3.19, U4.10
DIR2: U6.19, U7.10
DIR3: U9.19, U10.10
DTR: C4.1, J7.1
DTR1: C25.1, J17.1
DTR2: C38.1, J28.1
DTR3: C51.1, J39.1
GND: ADR.2, C1.2, C2.2, C3.-, C5.2, C7.2, C8.2, C9.2, C10.2, C12.2, C14.2, D2.C, D3.C, D4.C, D5.C, J1.1, J2.1, J3.GND, J3.P$4, J4.1, J5.6, J7.5, J7.6, J8.2, J9.P$2, J10.2, R7.2, R18.1, R19.1, R20.2, S1.1, S1.2, U1.3, U1.18, U1.29, U2.3, U2.5, U2.21, U44.2, Y1.2
GND1: ADR1.2, C13.2, C16.2, C17.2, C18.2, C19.2, C21.-, C22.2, C23.2, C24.2, C26.2, D7.C, D8.C, D9.C, D10.C, J12.GND, J12.P$4, J13.1, J14.1, J15.1, J16.6, J17.5, J17.6, J18.2, J19.2, J21.P$2, R13.1, R16.1, R17.2, R31.2, S2.1, S2.2, U3.3, U3.18, U3.29, U4.3, U4.5, U4.21, U5.2, Y2.2
GND2: ADR2.2, C27.2, C29.2, C30.2, C31.2, C32.2, C34.-, C35.2, C36.2, C37.2, C39.2, D12.C, D13.C, D14.C, D15.C, J23.GND, J23.P$4, J24.1, J25.1, J26.1, J27.6, J28.5, J28.6, J29.2, J30.2, J32.P$2, R35.1, R36.1, R37.2, R48.2, S3.1, S3.2, U6.3, U6.18, U6.29, U7.3, U7.5, U7.21, U8.2, Y3.2
GND3: ADR3.2, C40.2, C42.2, C43.2, C44.2, C45.2, C47.-, C48.2, C49.2, C50.2, C52.2, D17.C, D18.C, D19.C, D20.C, J34.GND, J34.P$4, J35.1, J36.1, J37.1, J38.6, J39.5, J39.6, J40.2, J41.2, J43.P$2, R52.1, R53.1, R54.2, R65.2, S4.1, S4.2, U9.3, U9.18, U9.29, U10.3, U10.5, U10.21, U11.2, Y4.2
INT: J11.1, R2.1, U2.24
INT0: J8.1, U2.32
INT1: J10.1, U2.1
INT2: J20.1, R25.1, U4.24
INT3: J18.1, U4.32
INT4: J19.1, U4.1
INT5: J31.1, R42.1, U7.24
INT6: J29.1, U7.32
INT7: J30.1, U7.1
INT8: J42.1, R59.1, U10.24
INT9: J40.1, U10.32
INT10: J41.1, U10.1
MISO: J5.1, U2.16
MISO1: J16.1, U4.16
MISO2: J27.1, U7.16
MISO3: J38.1, U10.16
MOSI: J5.4, U2.15
MOSI1: J16.4, U4.15
MOSI2: J27.4, U7.15
MOSI3: J38.4, U10.15
MS1: U1.9, U2.13
MS2: U1.10, U2.12
MS3: U1.11, U2.11
MS4: U3.10, U4.12
MS5: U3.11, U4.11
MS6: U3.9, U4.13
MS7: U6.10, U7.12
MS8: U6.11, U7.11
MS9: U6.9, U7.13
MS10: U9.10, U10.12
MS11: U9.11, U10.11
MS12: U9.9, U10.13
unnamed: D3.A, R11.1
unnamed: R7.1, R9.1, U44.4
unnamed: R19.2, U1.23
unnamed: R1.2, VIN.1
unnamed: JP6.1, R2.2
unnamed: ADR.1, U2.22
unnamed: D1.A, J3.VIN0, J9.P$1
unnamed: C6.1, U1.4
unnamed: C6.2, U1.5
unnamed: D5.A, R1.1
unnamed: R11.2, STEP.1
unnamed: D2.A, R12.1
unnamed: U2.7, Y1.1
unnamed: U2.8, Y1.3
unnamed: JP1.3, R6.2
unnamed: JP1.1, R8.2
unnamed: R12.2, SCK.1
unnamed: C15.1, U3.4
unnamed: R20.1, U1.13
unnamed: C10.1, U1.8
unnamed: C11.1, U1.6
unnamed: C15.2, U3.5
unnamed: R17.1, U3.13
unnamed: C19.1, U3.8
unnamed: C20.1, U3.6
unnamed: D4.A, R15.1
unnamed: 3V3.1, R15.2
unnamed: D10.A, R24.1
unnamed: R24.2, VIN1.1
unnamed: D6.A, J12.VIN0, J21.P$1
unnamed: D7.A, R26.1
unnamed: R26.2, STEP1.1
unnamed: U4.7, Y2.1
unnamed: U4.8, Y2.3
unnamed: D8.A, R29.1
unnamed: 3V1.1, R29.2
unnamed: JP4.1, R25.2
unnamed: R31.1, R32.1, U5.4
unnamed: R16.2, U3.23
unnamed: ADR1.1, U4.22
unnamed: D9.A, R27.1
unnamed: JP12.3, R33.2
unnamed: JP12.1, R34.2
unnamed: R27.2, SCK1.1
unnamed: C28.1, U6.4
unnamed: C28.2, U6.5
unnamed: R37.1, U6.13
unnamed: C32.1, U6.8
unnamed: C33.1, U6.6
unnamed: D15.A, R41.1
unnamed: R41.2, VIN2.1
unnamed: D11.A, J23.VIN0, J32.P$1
unnamed: D12.A, R43.1
unnamed: R43.2, STEP2.1
unnamed: U7.7, Y3.1
unnamed: U7.8, Y3.3
unnamed: D13.A, R46.1
unnamed: 3V2.1, R46.2
unnamed: JP15.1, R42.2
unnamed: R48.1, R49.1, U8.4
unnamed: R36.2, U6.23
unnamed: ADR2.1, U7.22
unnamed: D14.A, R44.1
unnamed: JP18.3, R50.2
unnamed: JP18.1, R51.2
unnamed: R44.2, SCK2.1
unnamed: C41.1, U9.4
unnamed: C41.2, U9.5
unnamed: R54.1, U9.13
unnamed: C45.1, U9.8
unnamed: C46.1, U9.6
unnamed: D20.A, R58.1
unnamed: R58.2, VIN3.1
unnamed: D16.A, J34.VIN0, J43.P$1
unnamed: D17.A, R60.1
unnamed: R60.2, STEP3.1
unnamed: U10.7, Y4.1
unnamed: U10.8, Y4.3
unnamed: D18.A, R63.1
unnamed: 3V4.1, R63.2
unnamed: JP21.1, R59.2
unnamed: R65.1, R66.1, U11.4
unnamed: R53.2, U9.23
unnamed: ADR3.1, U10.22
unnamed: D19.A, R61.1
unnamed: JP24.3, R67.2
unnamed: JP24.1, R68.2
unnamed: R61.2, SCK3.1
RXI: J7.3, U2.30
RXI1: J17.3, U4.30
RXI2: J28.3, U7.30
RXI3: J39.3, U10.30
SCK: J5.3, SCK.2, U2.17
SCK1: J16.3, SCK1.2, U4.17
SCK2: J27.3, SCK2.2, U7.17
SCK3: J38.3, SCK3.2, U10.17
SCL: J1.4, J2.4, J4.4, R8.1, U2.28
SCL1: J13.4, J14.4, J15.4, R34.1, U4.28
SCL2: J24.4, J25.4, J26.4, R51.1, U7.28
SCL3: J35.4, J36.4, J37.4, R68.1, U10.28
SDA: J1.3, J2.3, J4.3, R6.1, U2.27
SDA1: J13.3, J14.3, J15.3, R33.1, U4.27
SDA2: J24.3, J25.3, J26.3, R50.1, U7.27
SDA3: J35.3, J36.3, J37.3, R67.1, U10.27
STEP: STEP.2, U1.16, U2.26
STEP1: STEP1.2, U3.16, U4.26
STEP2: STEP2.2, U6.16, U7.26
STEP3: STEP3.2, U9.16, U10.26
TXO: J7.2, U2.31
TXO1: J17.2, U4.31
TXO2: J28.2, U7.31
TXO3: J39.2, U10.31
VIN: C1.1, C3.+, C8.1, C9.1, C11.2, D1.C, U1.22, U1.28, VIN.2
VIN1: C13.1, C17.1, C18.1, C20.2, C21.+, D6.C, U3.22, U3.28, VIN1.2
VIN2: C27.1, C30.1, C31.1, C33.2, C34.+, D11.C, U6.22, U6.28, VIN2.2
VIN3: C40.1, C43.1, C44.1, C46.2, C47.+, D16.C, U9.22, U9.28, VIN3.2

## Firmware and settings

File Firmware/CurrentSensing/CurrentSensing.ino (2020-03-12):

/*
  Tested with the following:
    Bench power supply, 12V, 2A max. https://www.sparkfun.com/products/retired/9291
    1.7A per phase stepper: https://www.sparkfun.com/products/10846

  Press a and z to raise or lower the voltage sent to stepper IC as the 'max' trip current voltage.

  To test large current loads, set to single step mode, step at 600, and raise the trip voltage to ~2V.
  This cause the motor to pull ~1A and heat the board significantly.

  Current through the coils depend heavily on the speed and step size.
  
  Speed 1000, Full Step
  tripVoltage of 550mV / 135mA
  650mV / 165mA
  1650mV / 489mA
  1750 / 526
  1850 / 555
  2350 / 731

  Speed: 900, Half Step
  550mV / 140mA
  650 / 180
  750 / 218
  1650 / 687
  1750 / 712
  1850 / 740
  2350 / 954
*/

#include <AccelStepper.h>

#define STEP  A3
#define DIRECTION 6
#define ENABLE 10
#define MS1 9
#define MS2 8
#define MS3 7

#define CURRENT_REFERENCE 5  //PWM capable pin
#define CURRENT_SENSE A6    //ADC pin

AccelStepper stepper(AccelStepper::DRIVER, STEP, DIRECTION);

int adc_out;
float VREF;
int OPAMP_GAIN = 23; //Designed to be 23 but varies with resistor tolerances.

enum stepOptions {
  STEP_SIZE_FULL = 0,
  STEP_SIZE_HALF,
  STEP_SIZE_QUARTER,
  STEP_SIZE_EIGHTH,
  STEP_SIZE_SIXTEENTH
};

#define numberOfSamples 32
int sense[numberOfSamples] = {0};
byte senseSpot = 0;

float runVoltage = 0.250;
int stepperSpeed = 300;

void setup()
{
  Serial.begin(115200);
  Serial.println("SparkFun Stepper Example");

  analogReference(INTERNAL); //Set AREF to 1.1V. This is pretty accurate at 1.098V measured.
  VREF = 1.1;

  pinMode(CURRENT_SENSE, INPUT);
  pinMode(ENABLE, OUTPUT);
  digitalWrite(ENABLE, LOW);

  pinMode(MS1, OUTPUT);
  pinMode(MS2, OUTPUT);
  pinMode(MS3, OUTPUT);

  setStepSize(STEP_SIZE_FULL);
  //setStepSize(STEP_SIZE_EIGHTH);

  stepper.setMaxSpeed(10000);
  stepper.setSpeed(stepperSpeed);

  analogWrite(CURRENT_REFERENCE, convertVoltageToPWM(runVoltage));

  Serial.println();
  Serial.println("a) Increase Itrip voltage");
  Serial.println("z) Decrease Itrip voltage");
  Serial.println("+) Increase Step speed");
  Serial.println("-) Decrease Step speed");
  Serial.println("0) Stop");
  Serial.println("1) Single step");
  Serial.println("2) Half Step");
  Serial.println("3) Quarter Step");
  Serial.println("4) Eighth Step");
  Serial.println("5) Sixteenth Step");
  Serial.println("r) Take current sense reading");

  Serial.print("Speed: ");
  Serial.print(stepperSpeed);
  Serial.print(" tripVoltage(Vref): ");
  Serial.println(runVoltage, 3);
}

void loop()
{
  if (Serial.available())
  {
    byte incoming = Serial.read();

    if (incoming == 'a')
    {
      runVoltage += 0.100;
      analogWrite(CURRENT_REFERENCE, convertVoltageToPWM(runVoltage));
    }
    else if (incoming == 'z')
    {
      runVoltage -= 0.100;
      if (runVoltage < 0.0) runVoltage = 0;
      analogWrite(CURRENT_REFERENCE, convertVoltageToPWM(runVoltage));
    }
    else if (incoming == '+')
    {
      stepperSpeed += 100;
      stepper.setSpeed(stepperSpeed);
      Serial.print("Speed: ");
      Serial.println(stepperSpeed);
    }
    else if (incoming == '-')
    {
      stepperSpeed -= 100;
      stepper.setSpeed(stepperSpeed);
      Serial.print("Speed: ");
      Serial.println(stepperSpeed);
    }
    else if (incoming == '0')
    {
      stepperSpeed = 0;
      stepper.setSpeed(stepperSpeed);
      Serial.print("Speed: ");
      Serial.println(stepperSpeed);
    }
    else if (incoming == '1')
    {
      setStepSize(STEP_SIZE_FULL);
      Serial.print("Step size: ");
      Serial.println("FULL");
    }
    else if (incoming == '2')
    {
      setStepSize(STEP_SIZE_HALF);
      Serial.print("Step size: ");
      Serial.println("HALF");
    }
    else if (incoming == '3')
    {
      setStepSize(STEP_SIZE_QUARTER);
      Serial.print("Step size: ");
      Serial.println("QUARTER");
    }
    else if (incoming == '4')
    {
      setStepSize(STEP_SIZE_EIGHTH);
      Serial.print("Step size: ");
      Serial.println("EIGHTH");
    }
    else if (incoming == '5')
    {
      setStepSize(STEP_SIZE_SIXTEENTH);
      Serial.print("Step size: ");
      Serial.println("SIXTEENTH");
    }
    else if (incoming == 'r')
    {
      //Take ADC reading
      senseSpot = 0;
      for (int x = 0 ; x < numberOfSamples ; x++)
      {
        adc_out = analogRead(CURRENT_SENSE);
        while (adc_out == 0)
          adc_out = analogRead(CURRENT_SENSE);

        sense[senseSpot++] = adc_out;
        senseSpot %= numberOfSamples;
        delay(1);
      }

      //      Serial.print("ADC: ");
      //      if (adc_out < 1000) Serial.print("0");
      //      if (adc_out < 100) Serial.print("0");
      //      if (adc_out < 10) Serial.print("0");
      //      Serial.print(adc_out);
      //      Serial.print("\t");

      int adcAverage = avgOfSamples();

      Serial.print("Avg: ");
      if (adcAverage < 1000) Serial.print("0");
      if (adcAverage < 100) Serial.print("0");
      if (adcAverage < 10) Serial.print("0");
      Serial.print(adcAverage);
      Serial.print("\t");

      float adcV = ((float)adcAverage + 0.5) / 1024.0 * VREF; //https://www.gammon.com.au/adc
      float adcA = adcV / 0.11 / OPAMP_GAIN;

      //adcA is per coil. If we want total coil consumption, *2.
      adcA *= 2;

      //  Serial.print("V: ");
      //  Serial.print(adcV, 3);
      //  Serial.print("\t");

      Serial.print("A: ");
      Serial.print(adcA, 3);
      Serial.print("\t");

      Serial.println();
    }
  }

  stepper.runSpeed();
}

int avgOfSamples()
{
  uint16_t sum = 0;

  for (int i = 0; i < numberOfSamples; i++)
    sum += sense[i];
  sum /= numberOfSamples;

  return sum;
}

//Takes a run or hold current of up to 2000(mA) and
//converts that to a PWM value where 1.7V = 2000mA
//1.7V / 3.3V = X / 255
uint8_t convertCurrentToPWM(uint16_t current)
{
  //int maxPWM = (uint32_t)170 * 255 / 330; //Assumes 3.3V system with 1.7V on stepper IC = 2A(max)
  //int maxPWM = (uint32_t)200 * 255 / 330; //Assumes 3.3V system with 2.0V on stepper IC = 2A(max)
  int maxPWM = (uint32_t)200 * 255 / 330; //Assumes 3.3V system with 2.7V on stepper IC = 2A(max)
  int pwmValue = map(current, 0, 2000, 0, maxPWM);
  Serial.print("pwmValue: ");
  Serial.println(pwmValue);

  float voltage = (pwmValue * 3.3 / 255.0) - 0.05;
  Serial.print("tripVoltage(Vref): ");
  Serial.println(voltage, 3);

  return (pwmValue);
}

//Takes a voltage and outputs it over PWM
uint8_t convertVoltageToPWM(float voltage)
{
  Serial.print("tripVoltage(Vref): ");
  Serial.print(voltage, 3);

  voltage += 0.05; //Add empirically found offset
  float pwmValue = voltage * 255.0 / 3.3;

  Serial.print(" pwmValue: ");
  Serial.println(pwmValue);

  return (pwmValue);
}

//Sets MS pins to user's input
void setStepSize(uint8_t stepSize)
{
  switch (stepSize)
  {
    case STEP_SIZE_FULL:
      digitalWrite(MS1, LOW);
      digitalWrite(MS2, LOW);
      digitalWrite(MS3, LOW);
      break;
    case STEP_SIZE_HALF:
      digitalWrite(MS1, HIGH);
      digitalWrite(MS2, LOW);
      digitalWrite(MS3, LOW);
      break;
    case STEP_SIZE_QUARTER:
      digitalWrite(MS1, LOW);
      digitalWrite(MS2, HIGH);
      digitalWrite(MS3, LOW);
      break;
    case STEP_SIZE_EIGHTH:
      digitalWrite(MS1, HIGH);
      digitalWrite(MS2, HIGH);
      digitalWrite(MS3, LOW);
      break;
    case STEP_SIZE_SIXTEENTH:
      digitalWrite(MS1, HIGH);
      digitalWrite(MS2, HIGH);
      digitalWrite(MS3, HIGH);
      break;
    default:
      digitalWrite(MS1, HIGH);
      digitalWrite(MS2, HIGH);
      digitalWrite(MS3, HIGH);
      break;
  }
}

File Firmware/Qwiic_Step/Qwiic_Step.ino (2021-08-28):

/*
  Firmware to drive Qwiic Step
*/

#include <Wire.h>
#include <EEPROM.h>
#include <AccelStepper.h> //Click here to get the library: http://librarymanager/All#AccelStepper by Mike McCauley
#include "registers.h"

#define DEVICE_ID 0x60
#define FIRMWARE_VERSION 0x0101
#define I2C_ADDRESS_DEFAULT 0x52
#define I2C_ADDRESS_FORCED 0x51
#define LOCATION_REGISTERMAP 0 //Location in EEPROM. Map is ~41 bytes currently.
#define LOCATION_PORSETTINGS 100 //Location in EEPROM for POR settings (for headless operation).

#define PRODUCTION_TARGET 1 //Uncomment to use the production code

//Hardware connections
#if defined(PRODUCTION_TARGET) //Used in production
const uint8_t PIN_STEP = A3;
const uint8_t PIN_ENABLE = 10;
const uint8_t PIN_DIRECTION = 6;
const uint8_t PIN_MS1 = 9;
const uint8_t PIN_MS2 = 8;
const uint8_t PIN_MS3 = 7;
const uint8_t PIN_ADDRESS = A7;
const uint8_t PIN_MAXCURRENT_PWM = 5;
const uint8_t PIN_CRRENT_SENSE = A6;
const uint8_t PIN_A49885_RESET = A0;
const uint8_t PIN_ESTOP_SWITCH = 2; //E-Stop
const uint8_t PIN_LIMIT_SWITCH = 3; //Limit switch
const uint8_t PIN_INT_OUTPUT = A1;
const uint8_t PIN_DEBUG = A2; //Routed to no where
#else //Used for development
const uint8_t PIN_DEBUG = A3;
const uint8_t PIN_STEP = 7;
const uint8_t PIN_DIRECTION = 8;
const uint8_t PIN_ENABLE = 10;
const uint8_t PIN_MS1 = 4;
const uint8_t PIN_MS2 = 5;
const uint8_t PIN_MS3 = 6;
const uint8_t PIN_MAXCURRENT_PWM = 11;
const uint8_t PIN_ADDRESS = 9;
const uint8_t PIN_ESTOP_SWITCH = 2; //E-stop
const uint8_t PIN_LIMIT_SWITCH = 3; //Limit switch
const uint8_t PIN_INT_OUTPUT = A1;
#endif

volatile memoryMap registerMap {
  DEVICE_ID,           //id
  FIRMWARE_VERSION,    //firmware
  {0, 0},              //interruptConfig {isReachedEnable, isLimitedEnable}
  {0, 0, 0, 0, 0, 0},  //motorStatus {isRunning, isAccelerating, isDecelerating, isReached, isLimited, eStopped}
  {0, 0, 0, 0, 0 , 1}, //motorConfig {ms1, ms2, ms3, disableMotorOnEStop, disableMotorOnPositionReached, stopOnLimitSwitchPress}
  {1, 0, 0, 0, 0},     //motorControl {runToPosition, runToPositionWithAccel, runContinuous, hardStop, disableMotor}
  0x00000000,          //currentPos
  0x00000000,          //distanceToGo
  0x00000000,          //move
  0x00,                //unlockMoveNVM
  0x00000000,          //moveTo
  0x00000000,          //maxSpeed (float)
  0x00000000,          //acceleration (float)
  0x00000000,          //speed (float)
  0x00,                //unlockSpeedNVM
  0x3F99999A,          //holdVoltage - 1.2V
  0x3F99999A,          //runVoltage - 1.2V
  I2C_ADDRESS_DEFAULT, //i2cAddress
};

//This memory map holds temporary "old" values so we don't call accelstepper functions an unnecessary amount of times
volatile memoryMap registerMapOld {
  DEVICE_ID,           //id
  FIRMWARE_VERSION,    //firmware
  {0, 0},              //interruptConfig {isReachedEnable, isLimitedEnable}
  {0, 0, 0, 0, 0, 0},  //motorStatus {isRunning, isAccelerating, isDecelerating, isReached, isLimited, eStopped}
  {0, 0, 0, 0, 0, 1},  //motorConfig {ms1, ms2, ms3, disableMotorOnEStop, disableMotorOnPositionReached, stopOnLimitSwitchPress}
  {1, 0, 0, 0, 0},     //motorControl {runToPosition, runToPositionWithAccel, runContinuous, hardStop, disableMotor}
  0x00000000,          //currentPos
  0x00000000,          //distanceToGo
  0x00000000,          //move
  0x00,                //unlockMoveNVM
  0x00000000,          //moveTo
  0x00000000,          //maxSpeed (float)
  0x00000000,          //acceleration (float)
  0x00000000,          //speed (float)
  0x00,                //unlockSpeedNVM
  0x3F99999A,          //holdVoltage - 1.2V
  0x3F99999A,          //runVoltage - 1.2V
  I2C_ADDRESS_DEFAULT, //i2cAddress
};

//This defines which of the registers are read-only (0) vs read-write (1)
memoryMap protectionMap = {
  0x00,               //id
  0x0000,             //firmware
  {1, 1},             //interruptConfig {isReachedEnable, isLimitedEnable}
  {1, 1, 1, 1, 1, 1}, //motorStatus {isRunning, isAccelerating, isDecelerating, isReached, isLimited, eStopped}
  {1, 1, 1, 1, 1, 1}, //motorConfig {ms1, ms2, ms3, disableMotorOnEStop, disableMotorOnPositionReached, stopOnLimitSwitchPress}
  {1, 1, 1, 1, 1},    //motorControl {runToPosition, runToPositionWithAccel, runContinuous, hardStop, disableMotor}
  (int32_t)0xFFFFFFFF,         //currentPos
  0x00000000,         //distanceToGo
  (int32_t)0xFFFFFFFF,         //move
  0xFF,               //unlockMoveNVM
  (int32_t)0xFFFFFFFF,         //moveTo
  (uint32_t)0xFFFFFFFF,         //maxSpeed (float)
  (uint32_t)0xFFFFFFFF,         //acceleration (float)
  (uint32_t)0xFFFFFFFF,         //speed (float)
  0xFF,               //unlockSpeedNVM
  (uint32_t)0xFFFFFFFF,         //holdVoltage
  (uint32_t)0xFFFFFFFF,         //runVoltage
  0xFF,               //i2cAddress
};

//Cast 32bit address of the object registerMap with uint8_t so we can increment the pointer
uint8_t *registerPointer = (uint8_t *)&registerMap;
uint8_t *protectionPointer = (uint8_t *)&protectionMap;
volatile uint8_t registerNumber; //Gets set when user writes an address. We then serve the spot the user requested.

nvmMemoryMap PORsettings = {
  0, //move
  0, //speed
  0, //i2cAddressState
};

//Interrupt turns on when position isReached, or limit switch is hit
//Turns off when interrupts are cleared by command
enum InterruptState
{
  INT_STATE_CLEARED = 0,
  INT_STATE_INDICATED,
};
volatile byte interruptState = INT_STATE_CLEARED;

//State machine for isReached bit within status register
//User can clear the isReached bit to clear the interrupt
//This allows for user to send multiple move commands and we'll not set the isReached bit until we reach the destination
enum MoveState
{
  MOVE_STATE_MOVING = 0,
  MOVE_STATE_NOTMOVING_ISREACH_SET,
  MOVE_STATE_NOTMOVING_ISREACH_CLEARED,
};
volatile byte moveState = MOVE_STATE_NOTMOVING_ISREACH_CLEARED;

//State machine for isLimited bit within status register
//User clears the isLimited bit to clear the interrupt
enum LimitState
{
  LIMIT_STATE_NOT_LIMITED = 0,
  LIMIT_STATE_LIMITED_SET,
  LIMIT_STATE_LIMITED_CLEARED,
};
volatile byte limitState = LIMIT_STATE_NOT_LIMITED;

//State machine for the I2C Address
//User can set via software command or hardware jumper
enum ADRState
{
  ADR_STATE_SOFTWARE = 0,
  ADR_STATE_JUMPER,
};
volatile byte adrState = ADR_STATE_SOFTWARE;

//State machine for the PWM Current
//We are either holding or running
enum PWMState
{
  PWM_STATE_HOLDING = 0,
  PWM_STATE_RUNNING,
};
volatile byte pwmState = PWM_STATE_RUNNING; //This should cause the device to go to HOLD state at POR
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

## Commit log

2019-11-12 temporary 4 layer
    [Qwiic-Step.brd, Qwiic-Step.sch]
2019-11-12 Reduce to 2 layers
    [Qwiic-Step.brd, Qwiic-Step.sch]
2019-11-12 Add git ignore. Remove # backups. Move hardware to sub dir.
    [Qwiic-Step.brd, Qwiic-Step.sch]
2019-11-12 Add INT pin. Remap ISP connector.
    [Qwiic-Step.brd, Qwiic-Step.sch]
2019-11-12 Add limit switches
    [Qwiic-Step.brd, Qwiic-Step.sch]
2019-11-13 New board layout. Added current sense.
    [Qwiic-Step.brd, Qwiic-Step.sch]
2019-11-19 Removed generated libraries and finishing up layout
    [Qwiic-Step.brd, Qwiic-Step.sch]
2019-11-19 Changes to polygon classes
    [Qwiic-Step.brd]
2019-11-20 Final board layout
    [Qwiic-Step-Panel.GBL, Qwiic-Step-Panel.GBO, Qwiic-Step-Panel.GBS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]
2019-12-09 Trying to get motor to turn
2019-12-13 Wrote printState and convertToFloat functions
    Reading/writing to struct does not work as expected when you are dealing with a float (setSpeed, maxSpeed, acceleration)
    [Qwiic_Step.ino, interrupts.ino]
2019-12-17 UpdateStepper function and interrupt handling
2019-12-20 Superficial function name changes and board update
    Rev 2 of Qwiic Step board! Fixed: MOSI was not connected to ISP pins! Adjusted MOSI and ADR jumper
    [Qwiic-Step.brd, Qwiic-Step.sch]
2020-01-07 got interrupt functionality working, but broke motor movement...
    Working on solidifying the correct logic for updateStepper() function. This is what actually controlls motor movement.
    [Qwiic-Step.sch]
2020-01-09 Move pin defs to hardware gates. Add comments. Remove unused var.
2020-01-09 Uppercase PIN constants.
2020-01-09 Mvoe function to helper tab. Print status with floats.
2020-01-09 Fix collision problems. Now compiles
    [interrupts.ino]
2020-01-10 Updated limit switch interrupt functionality
2020-01-10 Adding/testing stop on limit switch press functionality
2020-01-10 Prelim interrupts working.
2020-01-13 Move value correctly check when written to. Added stop ability is user writes move(0).
    [Qwiic_Step.ino, interrupts.ino]
2020-01-13 isReached is working well. Accel/decel now exhibiting correctly.
    [Qwiic_Step.ino]
2020-01-14 isLimited and isReached interrupts working
2020-01-14 Add mode changes based on motorcontrol register.
2020-01-14 Adding debounce to limit switch interrupt
2020-01-14 Fix bug in setSpeed function.
    [Qwiic_Step.ino]
2020-01-17 Move update of parameters and registers into interrupt to allow for clock stretching. Add disable output support.
2020-01-20 Enable pull up on int pin on dev board.
2020-01-20 Add state machine for I2C address jumper
2020-01-20 Correct accel/decel checks when motor is moving CCW.
    [Helpers.ino, updateRegisterMap.ino]
2020-01-21 Restart I2C if address is changed. Add hardStop() function. Correctly set disableMotor bit in case of EStop or isReached settings satisfied.
    [Helpers.ino, interrupts.ino, updateInterrupts.ino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]
2020-01-21 Add helper print functions to hold/run current registers.
2020-03-11 Update run with correct enable active low
    [run.ino]
2020-03-11 Add currentPWMControl and CurrentSense from hardwarechanges branch
2020-03-11 Pin name and value changes to get compatible with x02 hardware
2020-03-11 Workaround for lack of pullup on ADC7
    ADC6/7 have no internal pullups. ADC7 is checked as the ADR jumper at power up. Since pin is floating, we can do an ADC on the pin and see if it is zero (closed) or non-zero (floating / open). Not bullet proof but works.
    [Helpers.ino]
2020-03-11 Remove print gates
2020-03-11 Change resistor values on VIN and STEP LEDs.
    [Qwiic-Step.brd, Qwiic-Step.sch]
2020-03-11 Change pin numbers on current sensing sketch to match x02.
2020-03-11 Current sensing mostly working.
2020-03-12 Adding test menu to current sense sketch to make taking measurements easier.
2020-03-12 Increasing yellow LED resistor to 10k to limit brightness
    [Qwiic-Step.brd, Qwiic-Step.sch]
2020-03-12 Change CUR_REF_PWM RC filter to 100k/1uF.
    [Qwiic-Step.brd, Qwiic-Step.sch]
2020-03-19 Change PWM filter to use X7R rated cap.
    [Qwiic-Step.brd, Qwiic-Step.sch]
2020-03-19 Covert hold/run current to voltage.
2020-03-19 Fixed type conversion on run/hold voltage floats.
    [Helpers.ino, Qwiic_Step.ino]
2020-08-04 Update program_qwiic_step.bat
    Add fuse bits

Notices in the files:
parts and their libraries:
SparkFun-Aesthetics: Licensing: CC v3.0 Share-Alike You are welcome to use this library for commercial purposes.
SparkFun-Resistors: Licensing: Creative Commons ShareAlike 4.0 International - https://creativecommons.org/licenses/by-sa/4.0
